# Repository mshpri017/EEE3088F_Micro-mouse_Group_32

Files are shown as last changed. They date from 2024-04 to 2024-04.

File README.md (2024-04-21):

# EEE3088F_Micro-mouse_Group_32
This repository contains the  documentation for the assembly of a micro mouse - a tiny robot that navigates mazes. Find PCB designs, assembly guides, and all the info you need to make your own micro mouse.  The repo contains PCB Designs, Gerber files and Bill of Materials (BOM) for the Power and Sensing subsystems

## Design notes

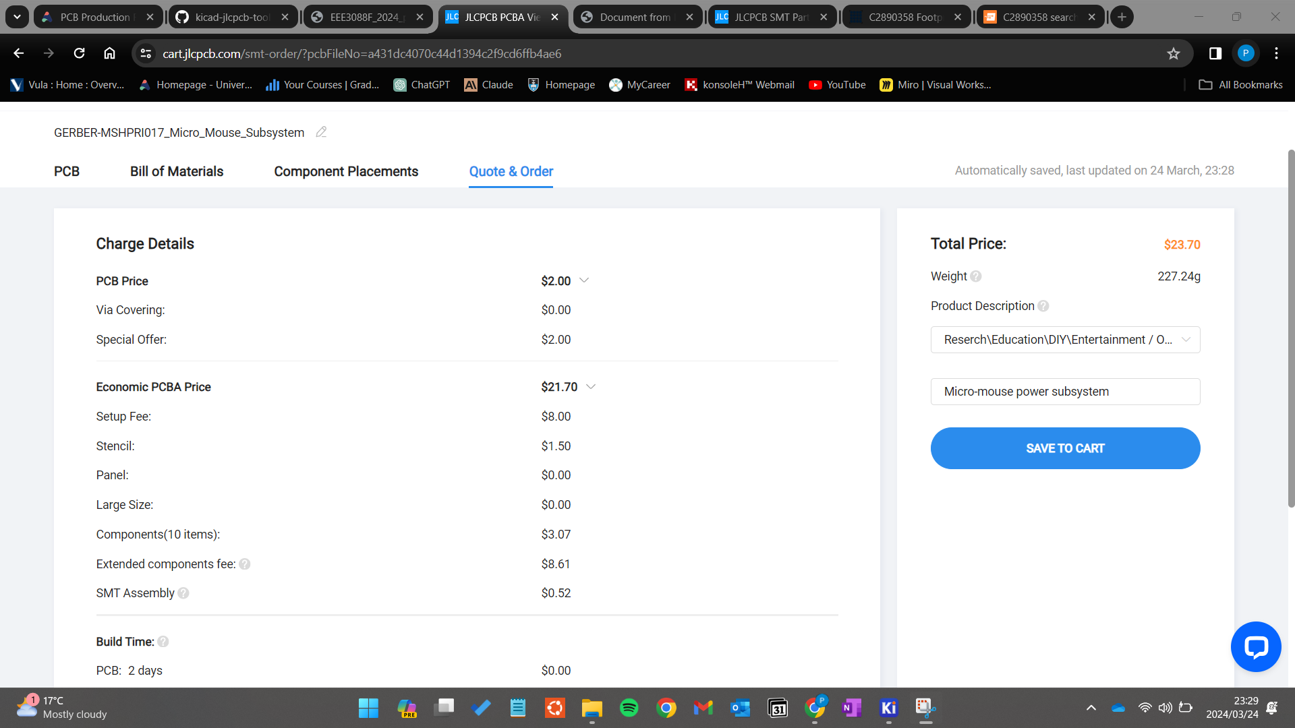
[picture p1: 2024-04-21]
Power Subsystem KiCad Files/jlcpcb/production_files/EEE3088F_Project_JLCPCBacceptance_MSHPRI017.png

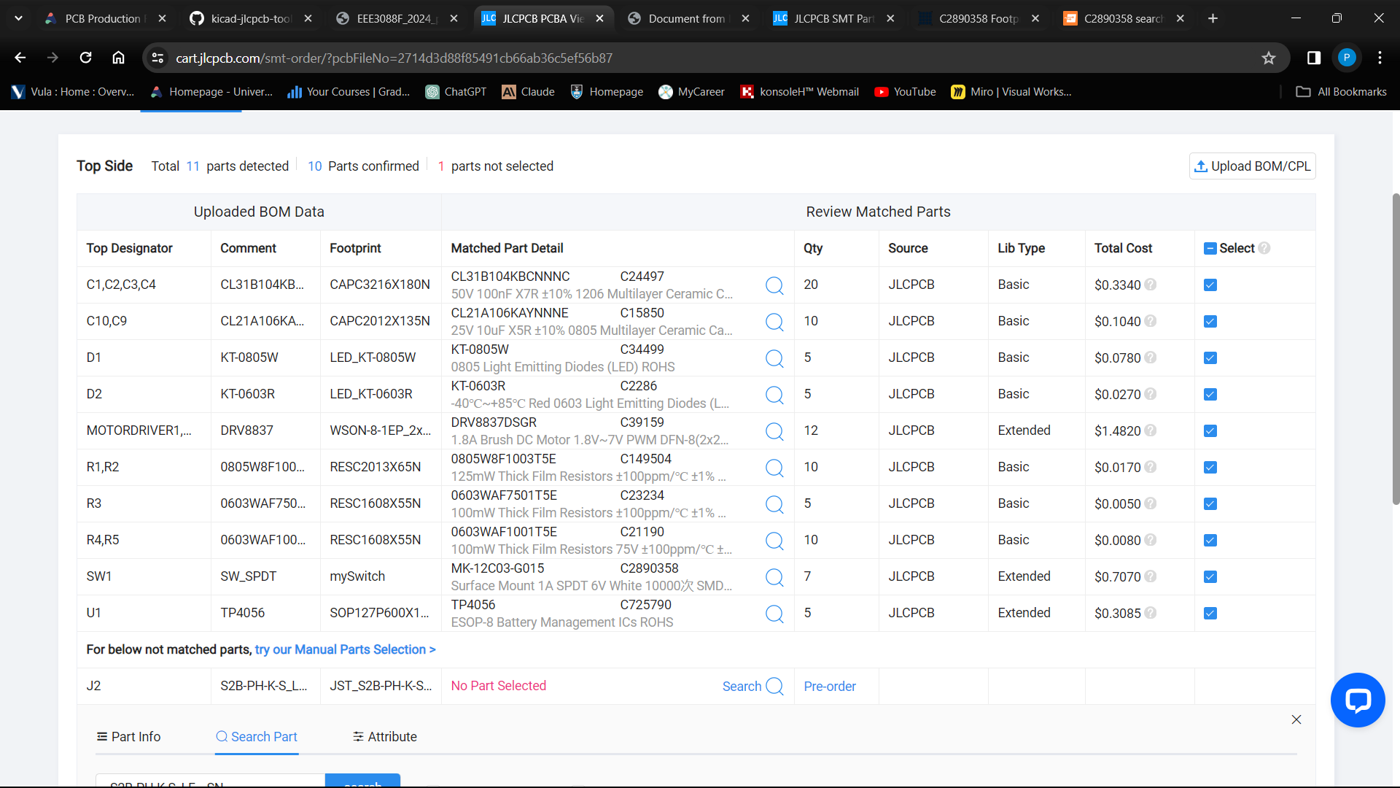
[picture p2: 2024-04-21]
Power Subsystem KiCad Files/jlcpcb/production_files/EEE3088F_Project_JLCPCBBOM_MSHPRI017.png

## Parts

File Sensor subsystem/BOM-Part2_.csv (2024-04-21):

Comment | Designator | Footprint | LCSC
100 | R1,R10,R11,R12,R2,R3,R4,R5,R6,R7,R8,R9 | R_0805_2012Metric_Pad1.20x1.40mm_HandSolder | C17414
SFH213 FA | PD1,PD2,PD3 | XDCR_SFH_213_FA | C2900211
MMBT2222A | Q1,Q2,Q3 | TO-92_Inline | C8512
TSAL4400 | D1,D2,D3 | LED_D3.0mm_Horizontal_O3.81mm_Z2.0mm | C94135

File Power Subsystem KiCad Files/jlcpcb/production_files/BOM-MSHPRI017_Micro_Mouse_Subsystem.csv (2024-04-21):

Comment | Designator | Footprint | LCSC
0805W8F1003T5E | R1,R2 | RESC2013X65N | C149504
CL21A106KAYNNNE | C10,C9 | CAPC2012X135N | C15850
0603WAF1001T5E | R4,R5 | RESC1608X55N | C21190
KT-0603R | D2 | LED_KT-0603R | C2286
0603WAF7501T5E | R3 | RESC1608X55N | C23234
CL31B104KBCNNNC | C1,C2,C3,C4 | CAPC3216X180N | C24497
SW_SPDT | SW1 | mySwitch | C2890358
KT-0805W | D1 | LED_KT-0805W | C34499
DRV8837 | MotorDriver1,MotorDriver2 | WSON-8-1EP_2x2mm_P0.5mm_EP0.9x1.6mm | C39159
TP4056 | U1 | SOP127P600X175-9N | C725790
S2B-PH-K-S_LF__SN_ | J2 | JST_S2B-PH-K-S_LF__SN_

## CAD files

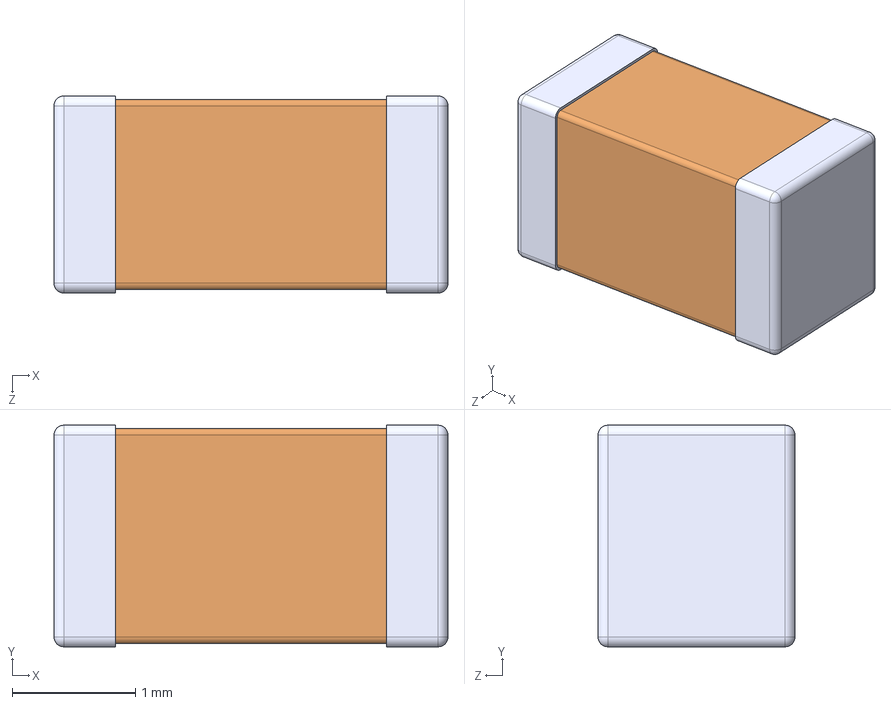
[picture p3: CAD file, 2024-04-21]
Power Subsystem Components/3D Models/CL31B104KBCNNNC.STEP
3.20 x 1.80 x 1.60 mm

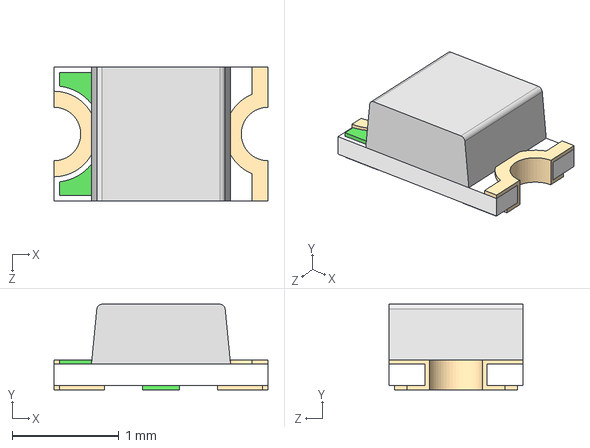
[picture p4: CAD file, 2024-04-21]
Power Subsystem Components/3D Models/KT-0805W--3DModel-STEP-269445.STEP
2.00 x 0.8 x 1.25 mm

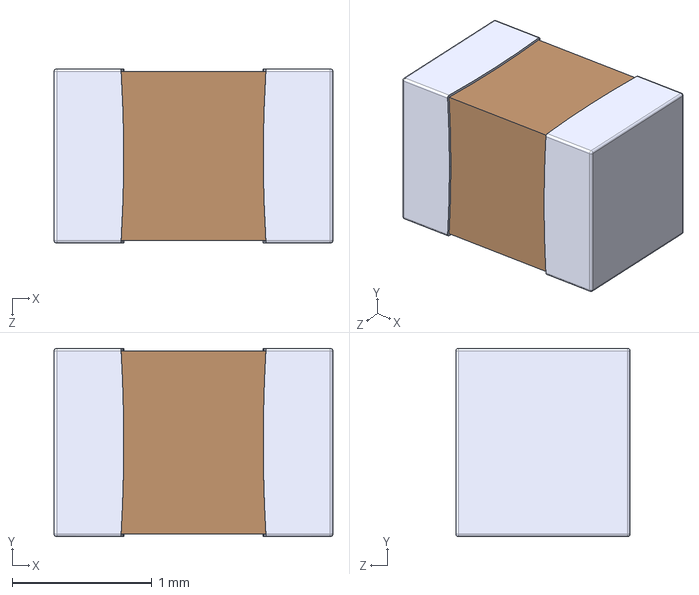
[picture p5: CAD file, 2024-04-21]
Power Subsystem Components/3D Models/CL21A106KAYNNNE.STEP
2.00 x 1.35 x 1.25 mm

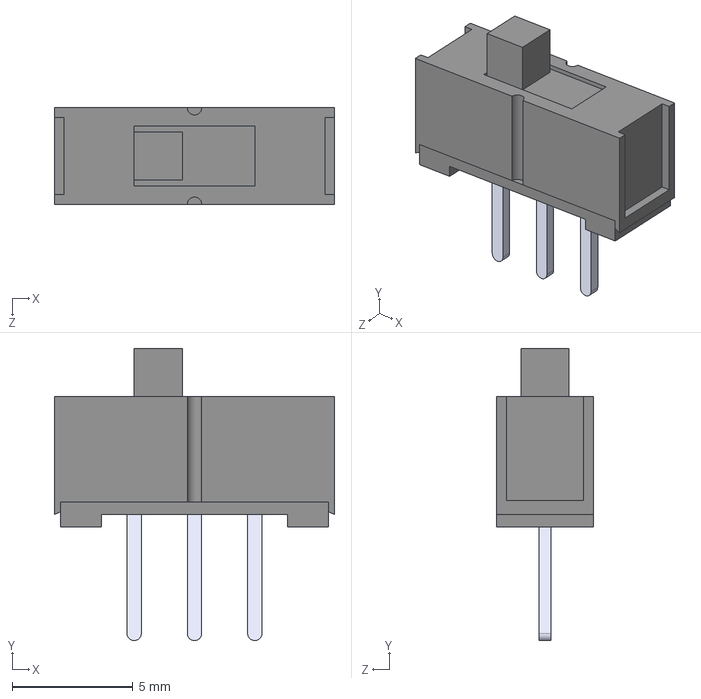
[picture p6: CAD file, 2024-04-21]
Power Subsystem Components/3D Models/MINI-SPDT-SW--3DModel-STEP-56544.STEP
11.6 x 12.1 x 4.00 mm

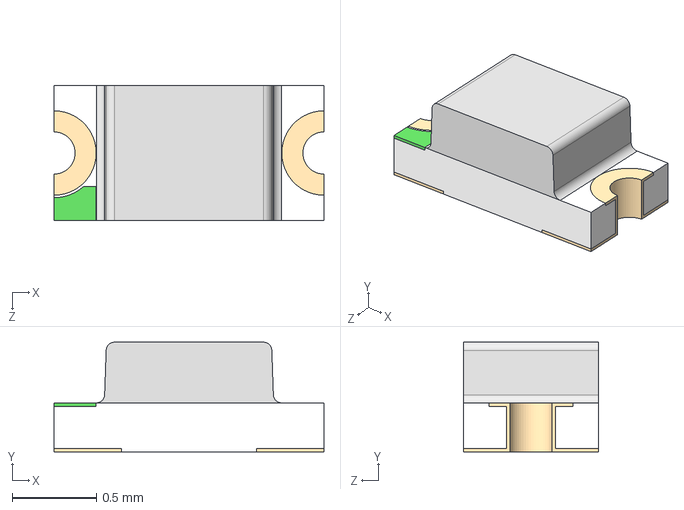
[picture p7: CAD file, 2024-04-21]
Power Subsystem Components/3D Models/KT-0603R--3DModel-STEP-269445.STEP
1.60 x 0.65 x 0.8 mm

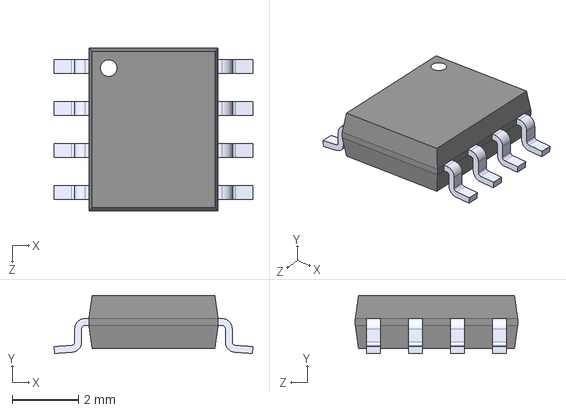
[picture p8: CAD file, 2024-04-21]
Power Subsystem Components/3D Models/TP4056--3DModel-STEP-56544.STEP
6.00 x 1.75 x 4.90 mm

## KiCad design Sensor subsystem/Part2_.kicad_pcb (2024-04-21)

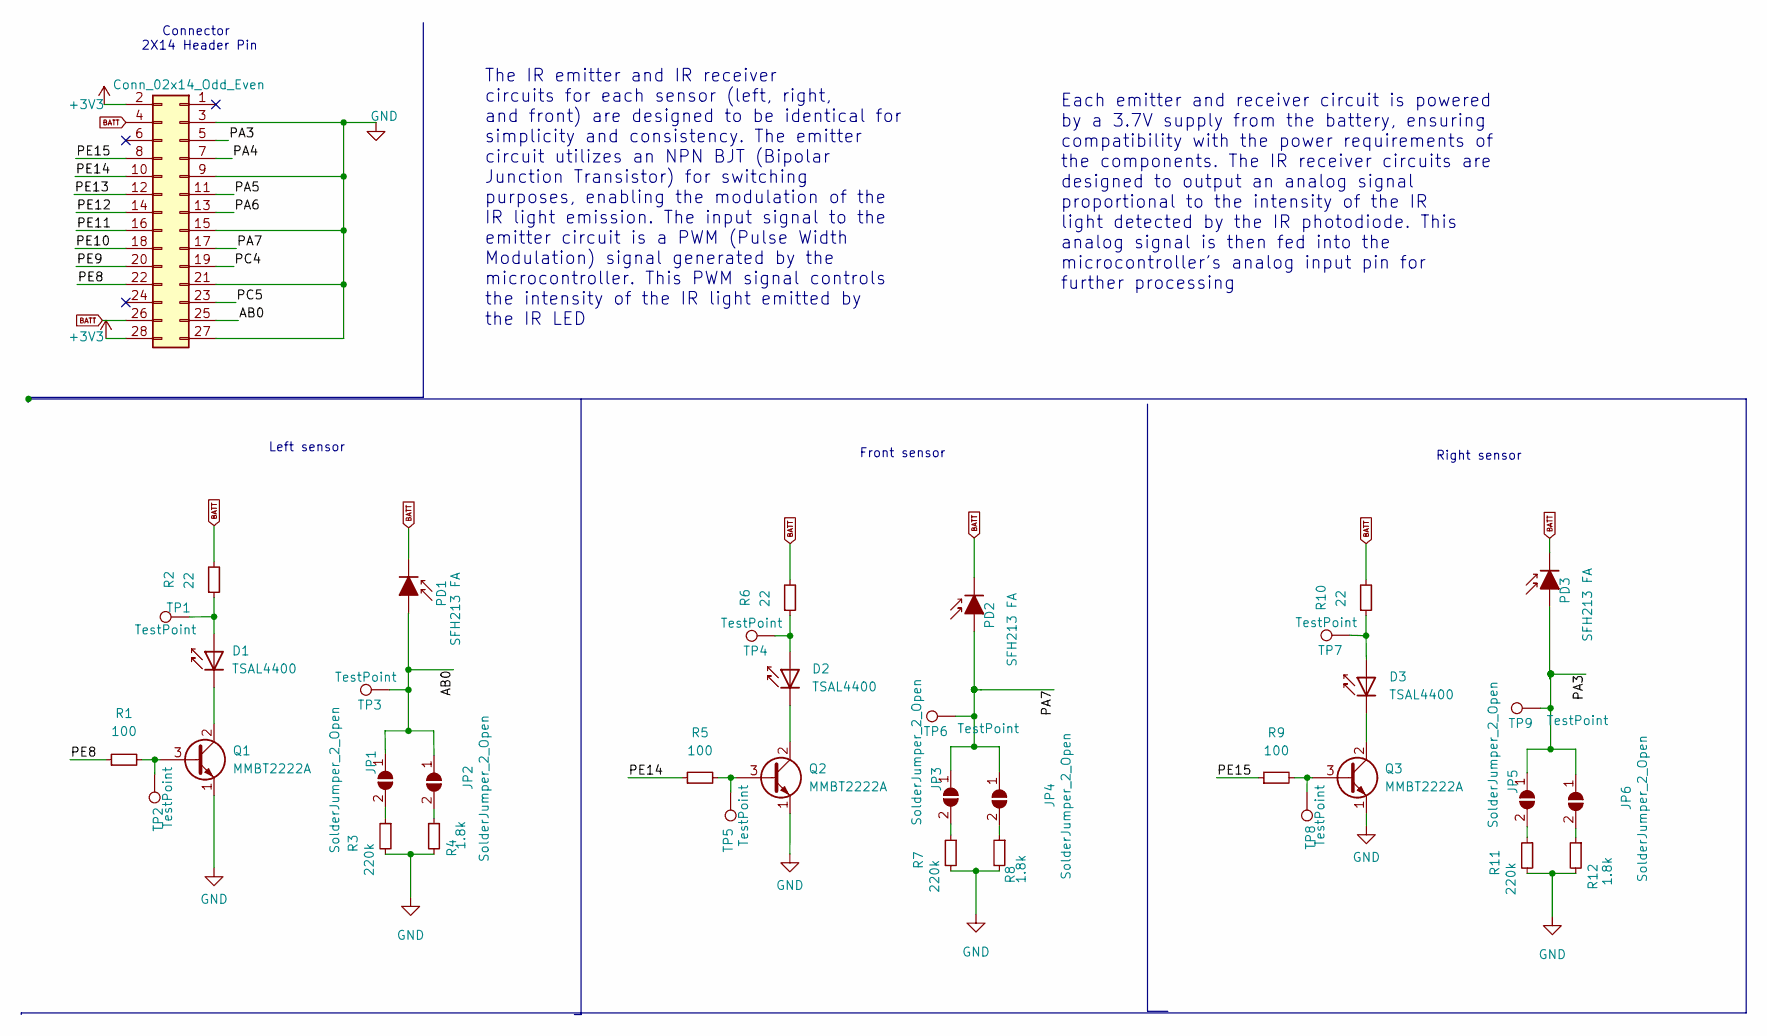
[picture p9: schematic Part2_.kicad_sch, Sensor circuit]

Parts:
D1, D2, D3: TSAL4400; LED_D3.0mm_Horizontal_O3.81mm_Z2.0mm
J1: Conn_02x14_Odd_Even; PinHeader_2x14_P2.54mm_Vertical
JP1, JP2, JP3, JP4, JP5, JP6: SolderJumper_2_Open; SolderJumper-2_P1.3mm_Open_TrianglePad1.0x1.5mm
PD1, PD2, PD3: SFH213 FA; XDCR_SFH_213_FA
Q1, Q2, Q3: MMBT2222A; TO-92_Inline
R1, R5, R9: 100; R_0805_2012Metric_Pad1.20x1.40mm_HandSolder
R2, R6, R10: 22; R_0805_2012Metric_Pad1.20x1.40mm_HandSolder
R3, R7, R11: 220k; R_0805_2012Metric_Pad1.20x1.40mm_HandSolder
R4, R8, R12: 1.8k; R_0805_2012Metric_Pad1.20x1.40mm_HandSolder
TP1, TP2, TP3, TP4, TP5, TP6, TP7, TP8, TP9: TestPoint; TestPoint_Pad_1.0x1.0mm

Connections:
+3V3: J1.2, J1.28
/AB0: J1.25, JP1.1 (A), JP2.1 (A), PD1.2 (A), TP3.1
/PA3: J1.5, JP5.1 (A), JP6.1 (A), PD3.2 (A), TP9.1
/PA4: J1.7
/PA5: J1.11
/PA6: J1.13
/PA7: J1.17, JP3.1 (A), JP4.1 (A), PD2.2 (A), TP6.1
/PC4: J1.19
/PC5: J1.23
/PE8: J1.22, R1.1
/PE9: J1.20
/PE10: J1.18
/PE11: J1.16
/PE12: J1.14
/PE13: J1.12
/PE14: J1.10, R5.1
/PE15: J1.8, R9.1
BATT: J1.4, J1.26, PD1.1 (K), PD2.1 (K), PD3.1 (K), R2.2, R6.2, R10.2
GND: J1.3, J1.9, J1.15, J1.21, J1.27, Q1.1 (E), Q2.1 (E), Q3.1 (E), R3.2, R4.2, R7.2, R8.2, R11.2, R12.2
unnamed: D1.1 (K), Q1.2 (C)
unnamed: D1.2 (A), R2.1, TP1.1
unnamed: D2.1 (K), Q2.2 (C)
unnamed: D2.2 (A), R6.1, TP4.1
unnamed: D3.1 (K), Q3.2 (C)
unnamed: D3.2 (A), R10.1, TP7.1
unnamed: JP1.2 (B), R3.1
unnamed: JP2.2 (B), R4.1
unnamed: JP3.2 (B), R7.1
unnamed: JP4.2 (B), R8.1
unnamed: JP5.2 (B), R11.1
unnamed: JP6.2 (B), R12.1
unnamed: Q1.3 (B), R1.2, TP2.1
unnamed: Q2.3 (B), R5.2, TP5.1
unnamed: Q3.3 (B), R9.2, TP8.1

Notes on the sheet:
Connector 2X14 Header Pin
Left sensor
Right sensor
The IR emitter and IR receiver circuits for each sensor (left, right, and front) are designed to be identical for simplicity and consistency. The emitter circuit utilizes an NPN BJT (Bipolar Junction Transistor) for switching purposes, enabling the modulation of the IR light emission. The input sig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
Each emitter and receiver circuit is powered by a 3.7V supply from the battery, ensuring compatibility with the power requirements of the components. The IR receiver circuits are designed to output an analog signal proportional to the intensity of the IR light detected by the IR photodiode. This an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
Front sensor

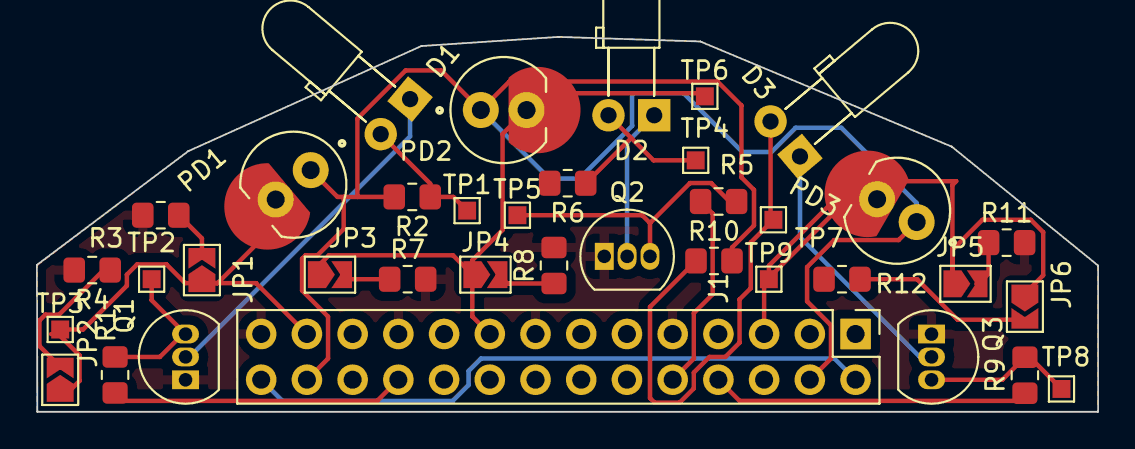
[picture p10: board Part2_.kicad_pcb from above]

Board: 2 copper layers, 59.0 x 20.8 mm, 37 parts (0 on the bottom side), 24 nets.

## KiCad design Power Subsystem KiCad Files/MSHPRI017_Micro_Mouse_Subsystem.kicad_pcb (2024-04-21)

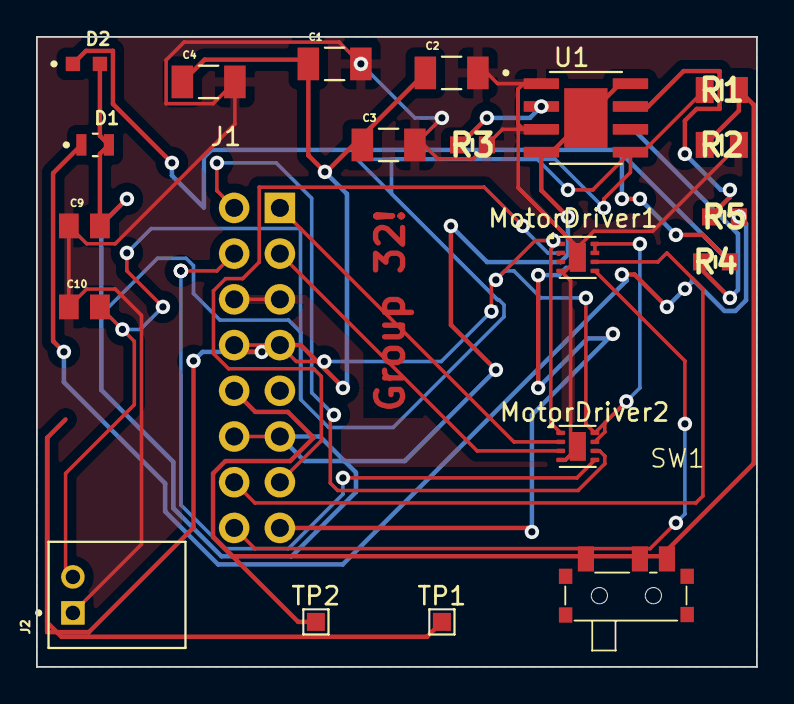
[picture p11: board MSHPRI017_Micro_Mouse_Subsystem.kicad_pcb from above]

Board: 2 copper layers, 40.0 x 35.0 mm, 21 parts (1 on the bottom side), 18 nets.

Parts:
C1, C2, C3, C4: CL31B104KBCNNNC; CAPC3216X180N
C9, C10: CL21A106KAYNNNE; CAPC2012X135N
D1: KT-0805W; LED_KT-0805W
D2: KT-0603R; LED_KT-0603R
J1: Conn_02x08_Odd_Even; PinHeader_2x08_P2.54mm_Vertical
J2: S2B-PH-K-S_LF__SN_; JST_S2B-PH-K-S_LF__SN_
MotorDriver1, MotorDriver2: DRV8837; WSON-8-1EP_2x2mm_P0.5mm_EP0.9x1.6mm
R1, R2: 0805W8F1003T5E; RESC2013X65N
R3: 0603WAF7501T5E; RESC1608X55N
R4, R5: 0603WAF1001T5E; RESC1608X55N
SW1: SW_SPDT; mySwitch
TP1, TP2: TestPoint; TestPoint_Pad_1.0x1.0mm
U1: TP4056; SOP127P600X175-9N

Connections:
5V_uC: C9.2, D1.A, D2.A, J1.11, J1.12, U1.4 (VCC), U1.8 (CE), U1.9 (EP)
Bat+: C10.2, J2.2, R1.1, SW1.1 (A), U1.5 (BAT)
Bat-: C1.2, C2.2, C3.2, C4.2, C9.1, C10.1, J1.5, J1.6, J2.1, MotorDriver1.4 (GND), MotorDriver1.9 (GND), MotorDriver2.4 (GND), MotorDriver2.9 (GND), R2.2, R3.2, U1.1 (TEMP), U1.3 (GND)
Batt: C1.1, C2.1, C3.1, C4.1, J1.7, J1.8, MotorDriver1.1 (VM), MotorDriver1.7 (~SLEEP), MotorDriver1.8 (VCC), MotorDriver2.1 (VM), MotorDriver2.7 (~SLEEP), MotorDriver2.8 (VCC), SW1.2 (B), TP1.1
Motor1_A: J1.13, MotorDriver1.2 (OUT1)
Motor1_B: J1.15, MotorDriver1.3 (OUT2)
Motor2_A: J1.1, MotorDriver2.2 (OUT1)
Motor2_B: J1.3, MotorDriver2.3 (OUT2)
unnamed: D1.C, R5.2
unnamed: D2.C, R4.2
unnamed: R3.1, U1.2 (PROG)
unnamed: R5.1, U1.7 (~CHRG)
unnamed: R4.1, U1.6 (~STDBY)
PWM1_A: J1.14, MotorDriver1.6 (IN1)
PWM1_B: J1.16, MotorDriver1.5 (IN2)
PWM2_A: J1.2, MotorDriver2.6 (IN1)
PWM2_B: J1.4, MotorDriver2.5 (IN2)
V_ADC: J1.10, R1.2, R2.1, TP2.1
